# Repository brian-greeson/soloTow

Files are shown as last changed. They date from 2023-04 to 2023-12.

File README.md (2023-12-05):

# SoloTow
An easy to assemble and inexpensive DIY winch for self towing paragliders. This project is still a work in progress.

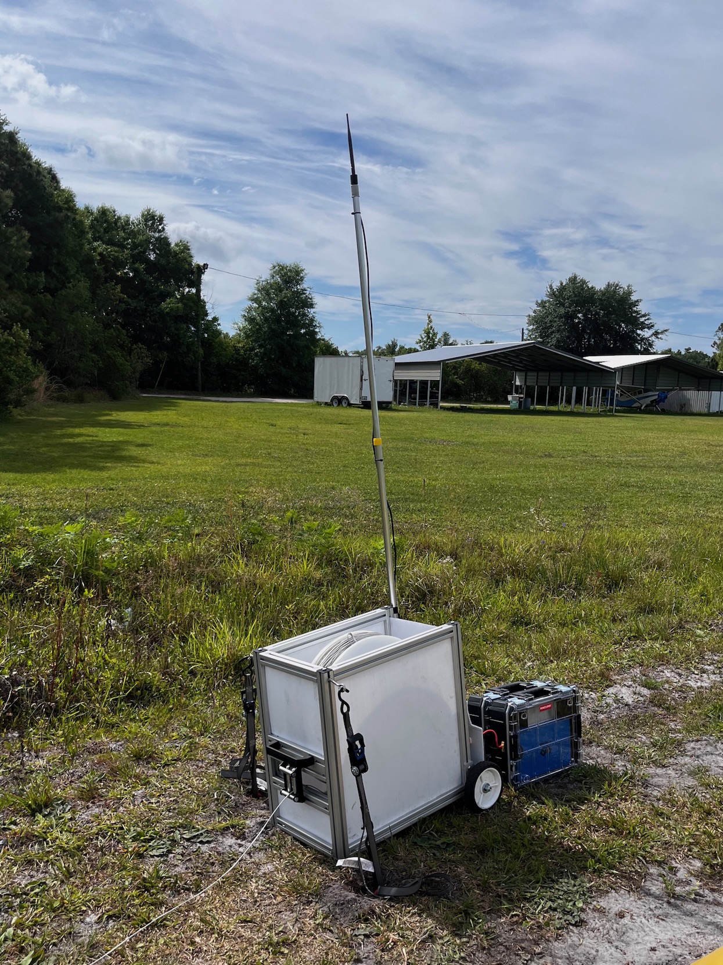
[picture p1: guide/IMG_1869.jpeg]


### **Obligatory Warning**
*Paragliding is dangerous. Towing is dangerous. Even when used in accordance with this guide; serious injury or death can occur when paragliding. This winch is not designed to be used by inexperienced pilots. No warranty is expressed or implied. Use at your own risk. Please seek professional instruction.*
## Introduction
Do you live in the flatlands? Tired of driving for hours to the nearest tow site, finding an extra vehicle and operator, or spending 5-10 thousand on a pay out winch? The SoloTow is the answer to all your paragliding woes. Every flight with the so This is a simple DIY winch for self towing paragliders. Cheap and portable enough for everyone to build and transport to the nearest suitable field. Construction materials are readily available. Assembly requires no special fabrication skills or tools. Currently some electronic knowledge and skills are required. If there is enough interest from the community I could make some partially assembled kits available that would remove the need for soldering and programming.
## Setting Expectations
What this design is:
- Designed to get an average solo paraglider pilot in the air, high enough to grab a nearby thermal for cross country flying. Expect 250m of altitude in lighter winds, 300-350m in optimal conditions. Able to be easily transported and setup in most places. Goal is to keep the complete build cost under 3k usd.

What this design isn't:
- This is not designed for club or commercial use, i.e. back to back towing all day long with no breaks for system to cool down. Nor to get you mega boosted, 1500m+ into the air. You are welcome to make modification to the design to have it suit your particular needs.
## Major Steps
* Select the configuration and parts for your build
* Order and assemble the mechanical parts
* Solder and assemble the electronics
* Connect the electronics
* Program the controllers and transmitter
* Test basic operation
* Spool the tow line onto the drum
* Field test
* Enjoy!
## Part selection
You have some choices to make when selecting parts for your winch. The most important choice is the motor and battery. These two components will determine the top speed, number of tows per charge, and maximum torque of your winch. These must be considered together. In general the higher the voltage of your system, the higher the maximum speed of the winch (not tension). The higher the "kilowatt" (Kw) of your system, the higher the maximum torque. The higher the amp hour rating (aH) of your battery the more tows per charge you will get. If you decide to use a higher Kw rated motor you must select a battery that can safely supply the extra power, else you may damage the battery and/or start a large lithium fire (not good). Many people get hung up on how many tows per charge. The batteries in the guide have enough energy to get an average pilot 4 tows.
In general I would recommend pilots of average size and lower elevations (1000m and below) build a 4.5Kw / 60 volt system. Pilots at higher elevations and average weight should opt for a 72v system. Those wishing to do more frequent towing may consider a 6Kw / 72 volt system. For reference I am a 80kg pilot flying a moderately fast wing at sea level. I have my 4Kw / 60 volt system and never use full power.
## Purchase links
Prices fluctuate so you may end up paying a little more/less that the prices listed below.
### Motor Bits
An average weight pilot will need a 3KW motor minimum. For example: I'm an 80kg pilot flying a moderately fast glider. I use the 4.5KW motor listed below and it works great. Heavier pilots should consider getting a 6KW or higher motor.
| Quantity | Item/Link| Price| Notes |
|:---:|:---:|:---:|:---:|
| 1 | [Brushless Hub Motor](https://kellycontroller.com/shop/brushless-hub-motor-13in/) | $479.00 | Select the 72 volt and at least the 4.5KW |
| 1 | [Motor Controller](https://kellycontroller.com/shop/kls-n/) | $229 | Select the KLS7230ND | 
| **Total** | | **$708.00** | |
### Battery
Be cautious with purchasing from vendors other than the ones listed here. Battery scams are rampant on aliExpress. I have purchased several batteries from this vendor and RMA'd a bad pack. The customer service was slow but good. If you want more tows per charge you can opt for a pack with a higher amp hour (Ah) rating. Or purchase multiple packs.
| Quantity | Item/Link| Price| Notes |
|:---:|:---:|:---:|:---:|
| 2 | [Battery](https://tinyurl.com/46wfumn2) | $452.80 | 60V 25Ah option |
OR
| 2 | [Battery](https://tinyurl.com/46wfumn2) | $612.00 | 72V 20Ah option |
|**Total**| | **$452.80** OR **$612.00**|

### Frame
The Frame is made of easy to source aluminum extrusion. I highly recommend purchasing the frame parts pre-cut and pre-drilled. The extra cost is negligible and it will save you a lot of time and frustration. 
Parts list Coming soon...

### Remote and Winch Controler
| Quantity | Item/Link| Price| Notes |
|:---:|:---:|:---:|:---:|
| 2 | [Lora Board](https://heltec.org/project/wifi-lora-32-v3/) | $17.90 | |
| 1 | [Potentiometer](https://a.co/d/56w9rYE) | $39.37 | |
| 1 | [Micro Switches](https://a.co/d/2vwkWf8) | $9.99| |
| 1 | [Latching Buttons](https://a.co/d/3Erq4vm) | $11.99 | |
| **Total**||**$97.15**|

### Ancillary Parts
| Quantity | Item/Link| Price| Notes |
|:---:|:---:|:---:|:---:|
| 1 | [Antenna Mast](https://a.co/d/f2BagqU) | $19.48 | You need Line of sight between the transmitter and receiver antenna. Ensure you get a mast tall enough to account for any obstructions at your tow area |
| 1 | [Antennas](https://a.co/d/8XnRbzk) | $13.99 |  |
|1| [Antenna Cable](https://a.co/d/dvxMuS1)| $15.99 | Get one a couple feet longer than your mast height |
| 1 | [Tow Line](https://tinyurl.com/2x9287e6) | $411.45 |  |
| 1 | [Drogue](https://towmeup.com/shop/ols/products/round-drogue-parachute) | $289.00 | One of the more expensive options. Let me know if you find a cheaper source |
|1 | [Fairlead](https://a.co/d/cL6a3BA) | $20.99| |
| 2 | [Wheels](https://a.co/d/hkvo3uy)| $29.99 ||
| 1 | [Winch Controller Box](https://a.co/d/iAHD5yw) | $14.98 | |
| 1 | [Winch Controller Battery](https://a.co/d/eulVu19) | $17.95 | |
| 1 | [Ground Anchors](https://a.co/d/alXvBq3) | $37.98 | |
|**Total**| | **$901.79**| |

### 3D Printed Parts
You can print these yourself using the files in this repository or you can purchase them pre-printed from the links below.
Parts list coming soon...

### Manufactured Parts
The drum flanges and motor brackets need to be cut from aluminum. You can use the files provided in this repository and have a local shop cut them. There are also many online services that can do this for you as well. I have had great work done by Xometry
Parts list coming soon...

| **Grand Total** | **$** | 
|:---:|:---:|

## Assembly
1. Assemble the winch frame.
2. Assemble the drum flange onto the hub motor.
3. Install the motor and controller on the winch frame.
4. Connect motor controller to hub motor and perform motor calibration.
5. Install winch controller on the winch frame and make connections.
6. Assemble the remote transmitter and hand controller.
7. Test the winch.
8. Spool the town line onto the winch.
9. Enjoy flying!

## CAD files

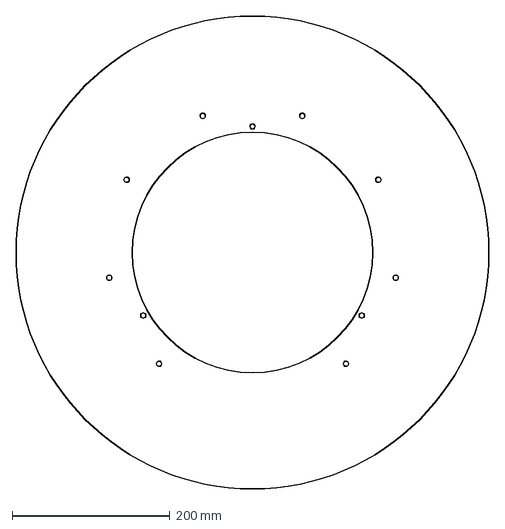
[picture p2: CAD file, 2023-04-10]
mechanical/drumflangev0.1.dxf
600.0 x 600.0 mm

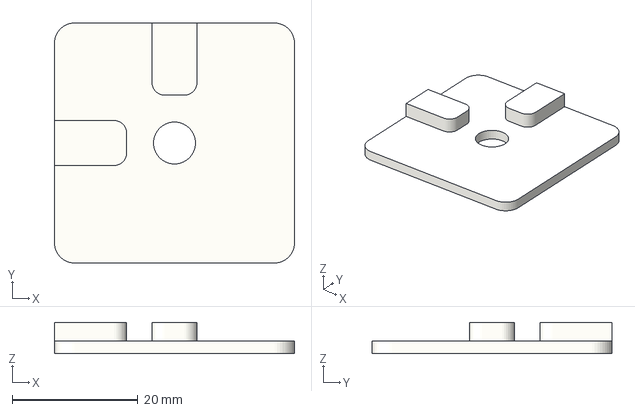
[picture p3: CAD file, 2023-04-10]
mechanical/printed/accessories/endcap.3mf
38.1 x 38.1 x 5.00 mm

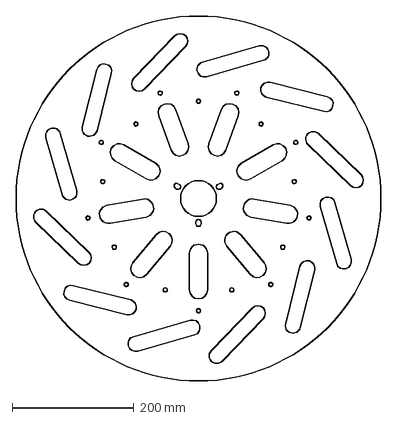
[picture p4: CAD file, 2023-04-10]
mechanical/drumflangeBoltv0.1.dxf
600.0 x 600.0 mm
